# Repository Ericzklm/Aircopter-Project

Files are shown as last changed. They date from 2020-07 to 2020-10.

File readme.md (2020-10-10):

# Aircopter Project

#### To see a more updated version of this project, see Aircopter-Project-v2

This project was done in association with the IEEE Student Branch on the UCLA campus.
This is the first iteration of the project.

The goal of the project was to: 1. Design and assemble a custom PCB for a drone,
2. Write a program to hover the drone, then fly the drone. Because of the nature
of the project, the PCB was required to be small and compact (meaning SMD soldering
was needed) and the program needed to be quick and responsive.

### Hardware Selection Choices:

**MCU**: The main chip is the model STM32F405. This was chosen for its ideal balance
between size and functionality. It is able to support all the needed sensors and
motor drivers for our drone and can be powered by a 3.3v supply which closely
matches the 3.7v of standard drone batteries (3.7v is stepped down to 3.3 using
a voltage regulator). Additionally, this chip was more ideal than other chips of
similar style because it handles floating point calculations better which allows
for simplicity and efficiency when writing the program.

**Voltage Regulator**: The voltage regulator used is the Richtek RT6150B-33GQW which
was choosen for its size and the use of buck-boost as well as operating within
the voltage supplied by the battery. The voltage regulator was simple to use
and had a well documented spec sheet in comparison to other choices but used
exposed pads instead of pins for soldering which proved to be the biggest
challenge in assembly.

**Wireless Module**: The wireless module used is the nrf24l01 which is standard, easy
to use, and familiar so we used it in this application since it fits well with the
acclerometer module.

**Accelerometer/Gyroscope**: The module used is the mpu6050 which is standard, easy to
use, and familiar so we used it in this application since it fits well with the
wireless module.

**Oscillator**: The oscillator used is the Abracon ABLS-12.000MHZ-B2-T which is a
crystal oscillator at 12 mHz which was suitable for the MCU. This specific oscillator
was choosen because the documentation was clear on how to configure the module. A
SMD mounted version was chosen.

**Passive Components**: For the resistors, capacitors, and inductors, we primarily
used parts with the package size 0603 which would fit the board without being
overly difficult to solder. Each piece was checked for its operating voltages as 
well as the operating temperatures to make sure no issues would arise.

### Hardware Design Choices:

**General**: The board is composed of two sides where each side has routes and vias to
connect the different components. The negative spaces are occupied by polygons. On
the front side, there is a seperate polygon for 3.7v and 3.3v that are connected
by the voltage regulator that steps the voltage down. On the back, there are seperate
polygons for ground and motor ground. Motor ground is seperated because the motor
ground will have more noise and we dont want to include the added noise in other
components.

**Battery**: The battery is a generic 3.7v drone battery that connects via a JST connector.
A couple of decoupling capacitors are placed directly alongside the female header on the 
board. It is placed as close as possible to the JST headers that connect to the motors
as we need to decrease the resistance by having a large polygon that gives a direct
connection.

**Voltage Regualtor**: The voltage regulator is placed between the 3.7v and 3.3v planes
such that the two are completely isolated. There is an inductor included directly
alongside the voltage regulator as recommended by the spec sheet. A few decoupling
capcitors are also included.

**Voltage Divider**: A couple resistors are used to form a voltage divider that gives
an analog input to the MCU which can be used to read battery status. These resistors
are placed such that they do not have signficant effect on the routing or the polygons.

**Programmer**: The programmer is a set of 4 male header pins that allow us to upload 
programs to the drone through a seperate board. It is placed in the top left corner
for easy access and to make sure the sensors do not cover the pins.

**Reset Button**: The switch is placed such that there is easy access to it while not having
the placement disrupt any polygons. A capacitor is included to stabalize the signal sent
to the MCU.

**Oscillator**: The oscillator is placed as close to the MCU as possible to reduce unwanted
affects on the traces. As indicated by the spec sheet, there are two resistors that
ground both the input and output of the oscillator.

**Motors**: The motors connectorsare placed along the top of the board for easy access when 
plugging in the JST connectors. Each motor is paired with a motor driver circuit including
a diode and a mosfet. These components are located as close as possible to each other and 
have the thickest possible traces to decrease resistance. Each motor driver is connected
to a PWM capable pin located on the MCU.

**MCU**: The MCU is placed in a central position on the board as it needs to connect to most
components on the board. It is turned such that the length of traces is optimized and
components that are more essential to have short traces are accounted for. The decoupling
capacitors for the MCU are located on the opposite side of it and are connected by vias.

**Sensor Modules**: Both modules are lifted above the board using headers and because they
sit at similar heights above the board, their placement does not overlap. The decoupling
capacitors are placed near the respective pins on the MCU.

### Hardware Flaws:

**Not Space Efficient**: A few choices made the board more cluttered and more difficult to
make routes and polygons. The motor driver circuits could have made better use of the
two sided board as in the current configuration, they occupied a quarter of the board.
The oscillator would have benefitted from being a through-hole component as the soldering
pads and capacitors occupied a lot of space. In a different part of the board. There is
a lot of open space meaning there are parts of the board where there are unnecessary
bottlenecks.

**Accelerometer Placement**: The idea behind the accelerometer and wireless module not
overlapping is that since they were both lifted off the main board at a similar height,
they could not occupy the same space. However, the accelerometer lies slightly lower
than the wireless module so it can be moved closer the the MCU, allowing for shorter
traces.

**Bottlenecks**: There are some moderate bottlenecks in this design and also places where
the polygons have rather indirect routes. For example, some components rely on power
that comes gaps in the MCU which signficantly bottlenecks the polygons. The 3.3v 
needed by the wireless module comes from a couple vias and a route used as a bridge
rather than having a direct connection as it is cut off from the 3.3v polygon.

**Voltage Regulator**: The voltage regulator was small and simple but due to the exposed
pad design and its small size, was a pain to solder. This ended up being by far the
biggest hiccup in the assembly of the board and required backup components.

**Decoupling Capacitors**: The decoupling capacitors are not optimally placed in every
case but rather are placed to prevent bottlenecks. Capacitors for certain components
are placed near the MCU rather than the component itself.

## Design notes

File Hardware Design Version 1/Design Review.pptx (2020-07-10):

## Design Review

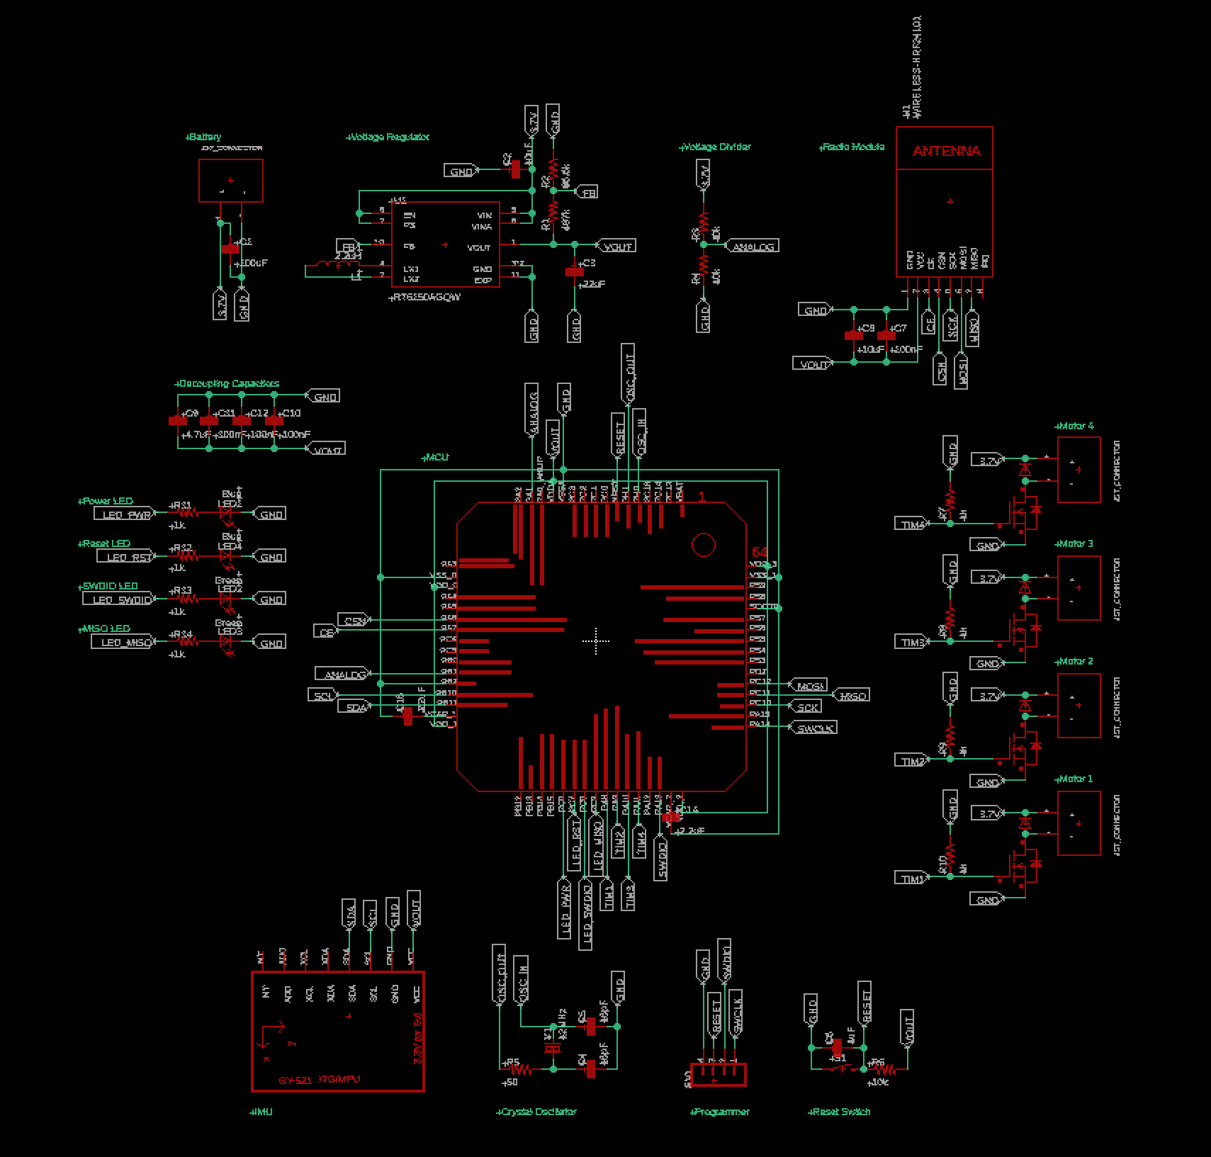
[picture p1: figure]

Team #6

## Parts

Programmer
Oscillator/resonator: ABLS-12.000MHZ-B2-T
Voltage regulator
Decoupling capacitors
Reset switch

Battery: 3.7 Volts
Voltage divider
Radio module: NRF24L01p
IMU: MPU6050
Motor driver (x4)
MCU: STM32F405RGT6

## Battery

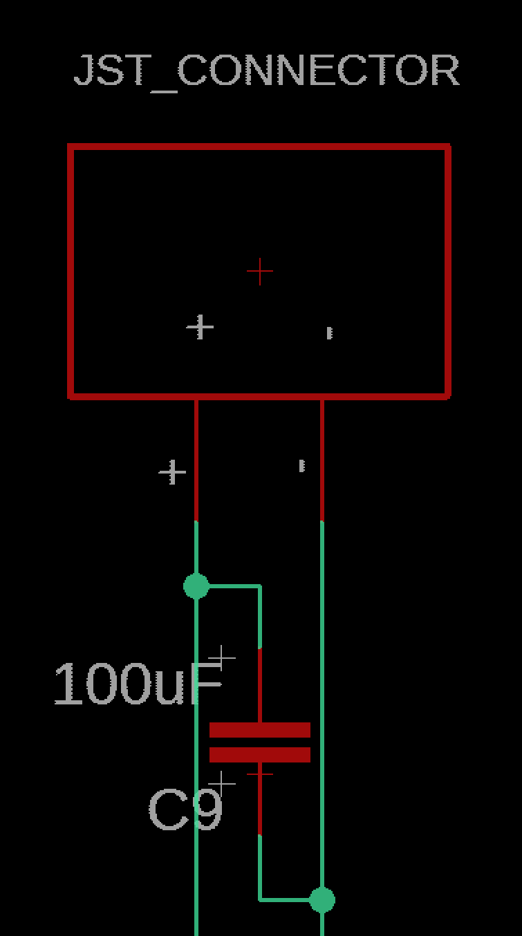
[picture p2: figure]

3.7 V
100 uF Decoupling Capacitor

## Voltage Divider

Resistors: 10kOhm (x2)
Attached to an analog pin
Receives power from the battery

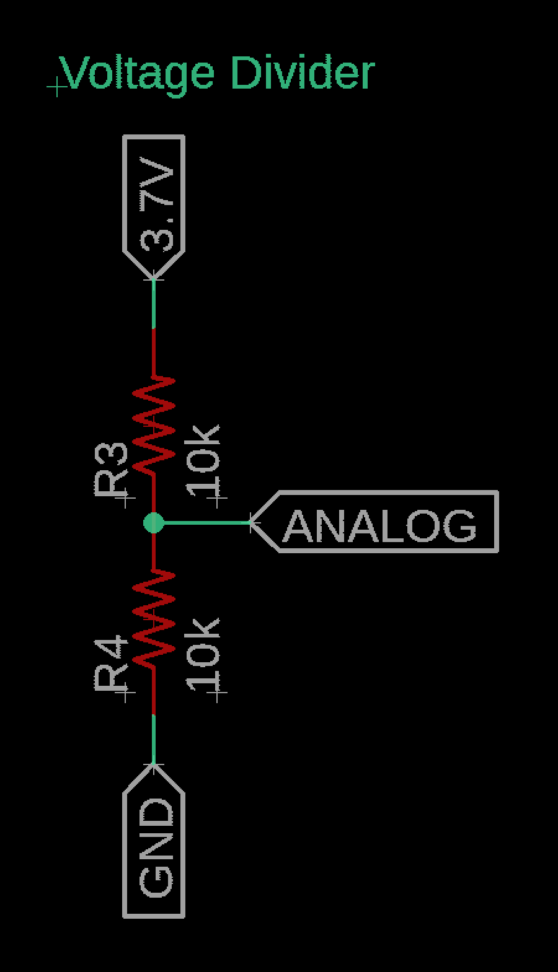
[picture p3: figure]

## Radio Module

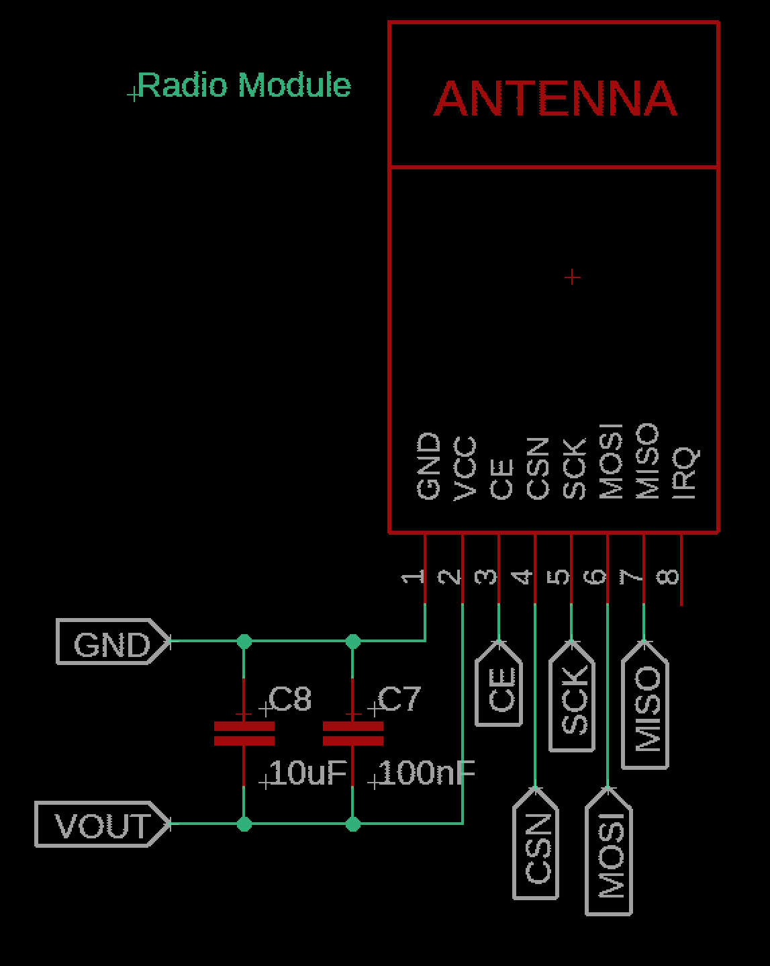
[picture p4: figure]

NRF24L01p
Decoupling Capacitors: 10uF, 100nF

## IMU

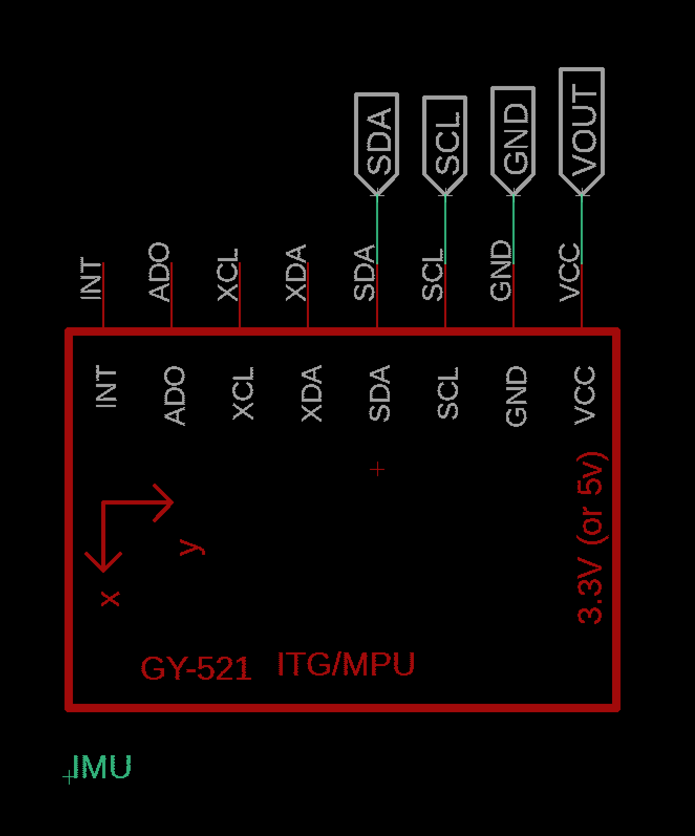
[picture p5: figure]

MPU6050

## Motor Driver

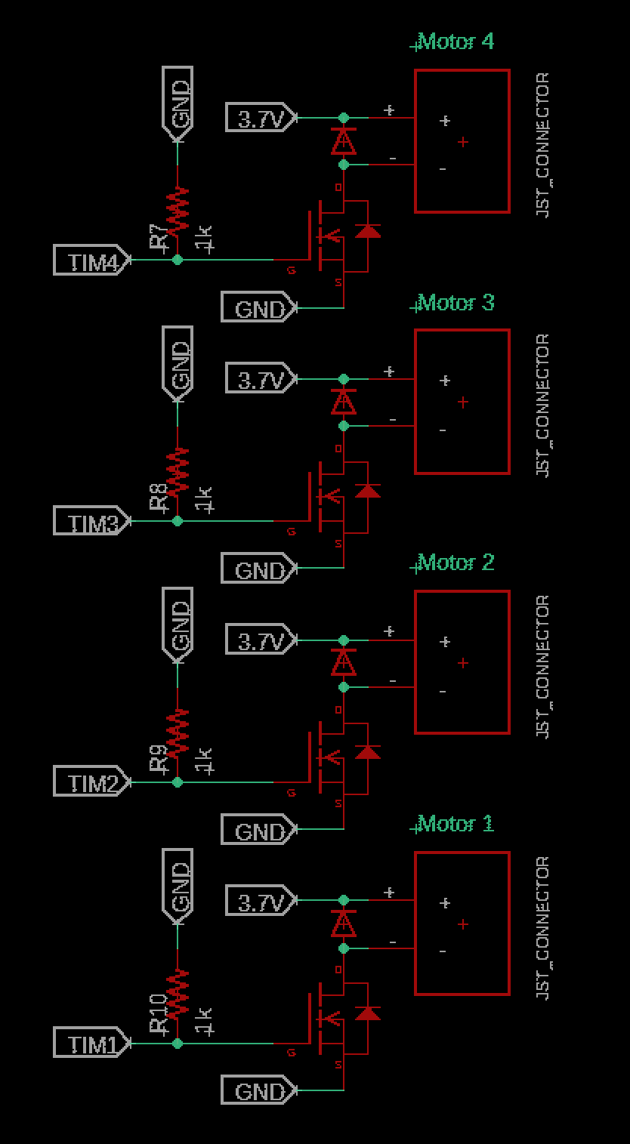
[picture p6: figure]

MOSFET: Infineon IRLML6244TRPBF (x4)
Diode: Panasonic DB2W40300L (x4)
Resistor: 1kOhm (x4)

## MCU

STM32F405RGT6

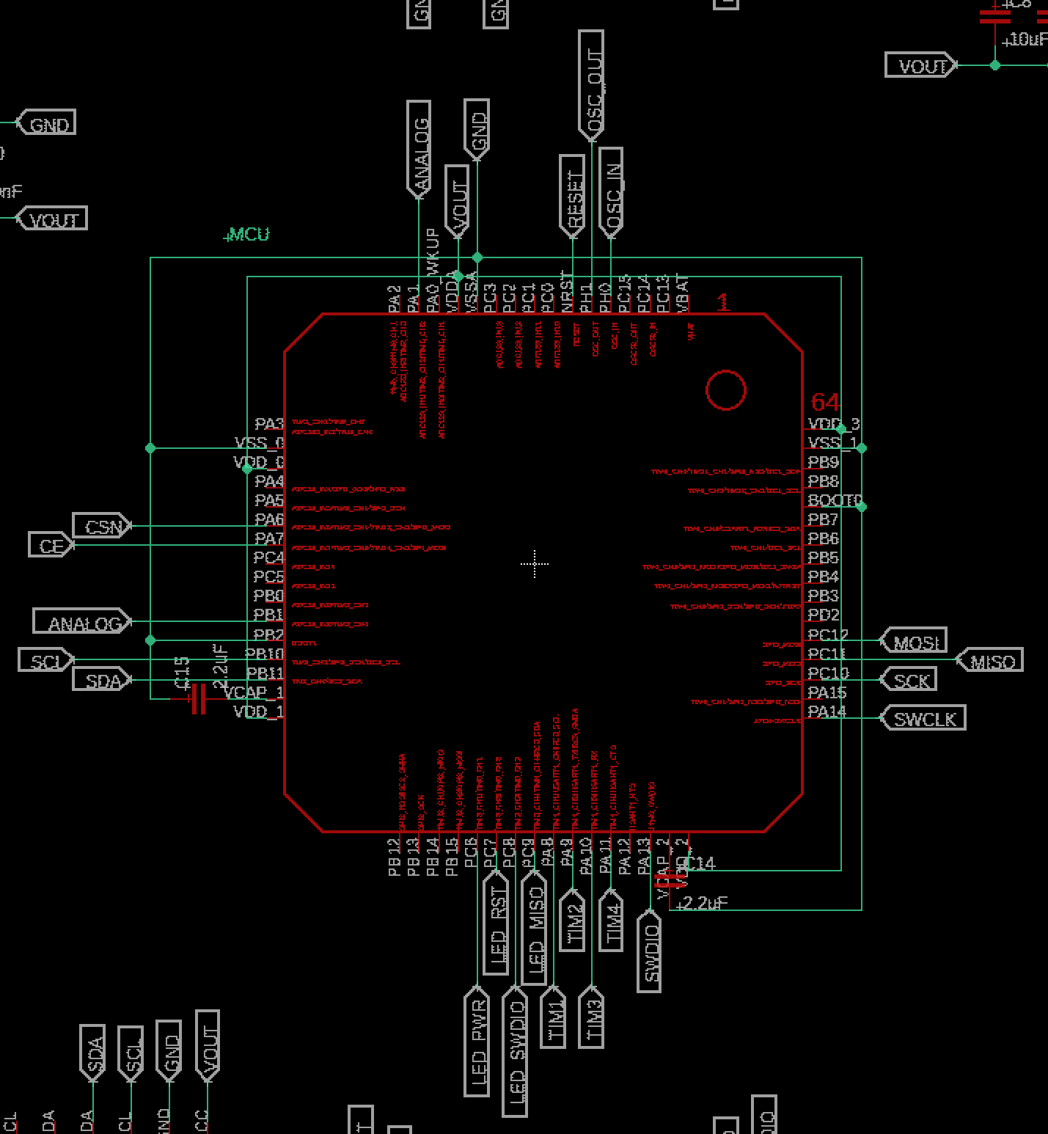
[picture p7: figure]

## Programmer

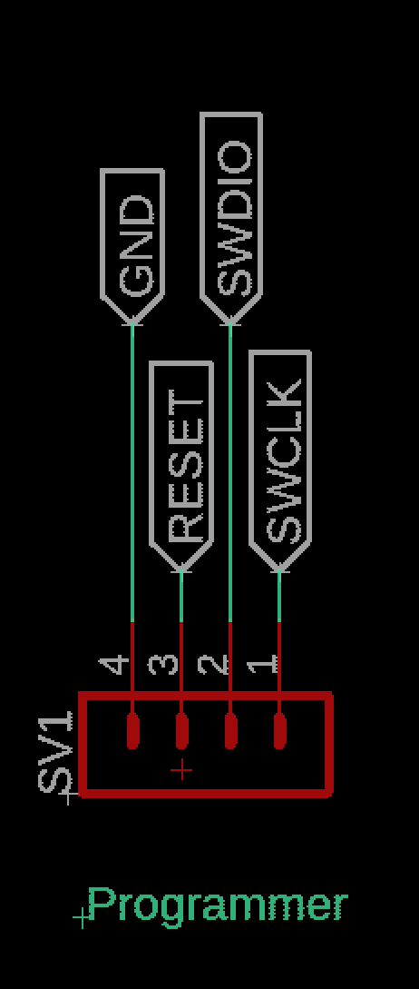
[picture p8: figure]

## Crystal Oscillator

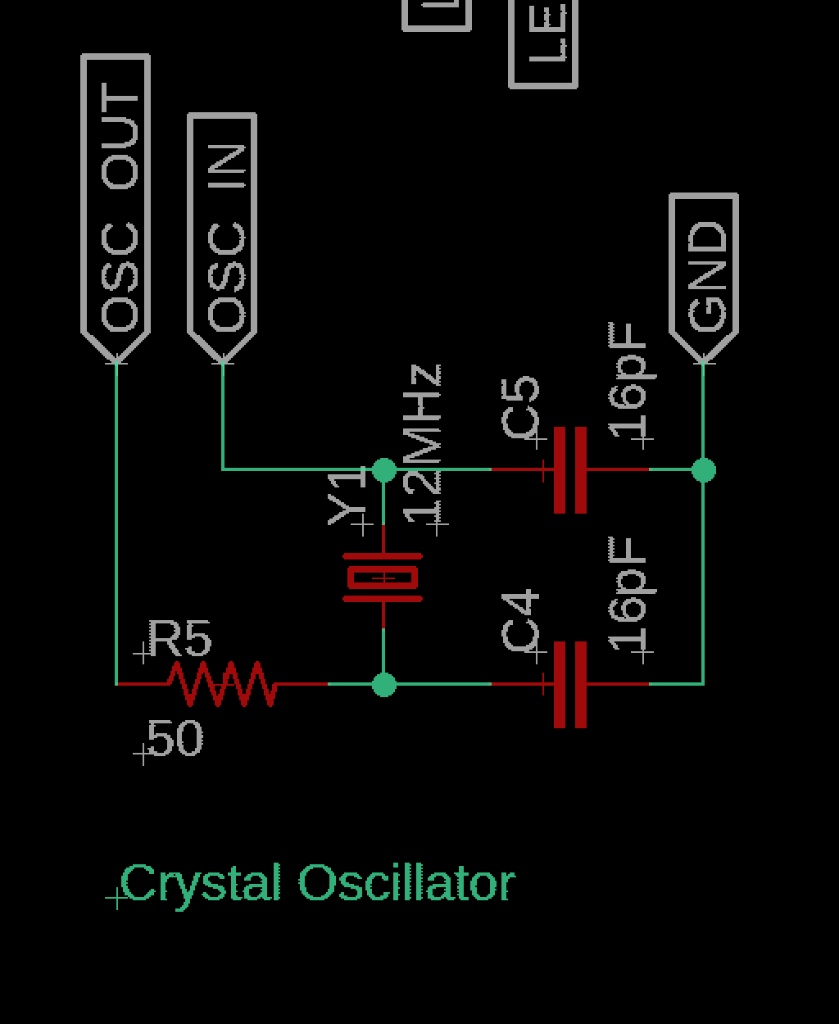
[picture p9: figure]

Abracon ABLS-12.000MHZ-B2-T
Capacitor: 16pF (x2)
Resistor: 50Ohm

## Voltage Regulator

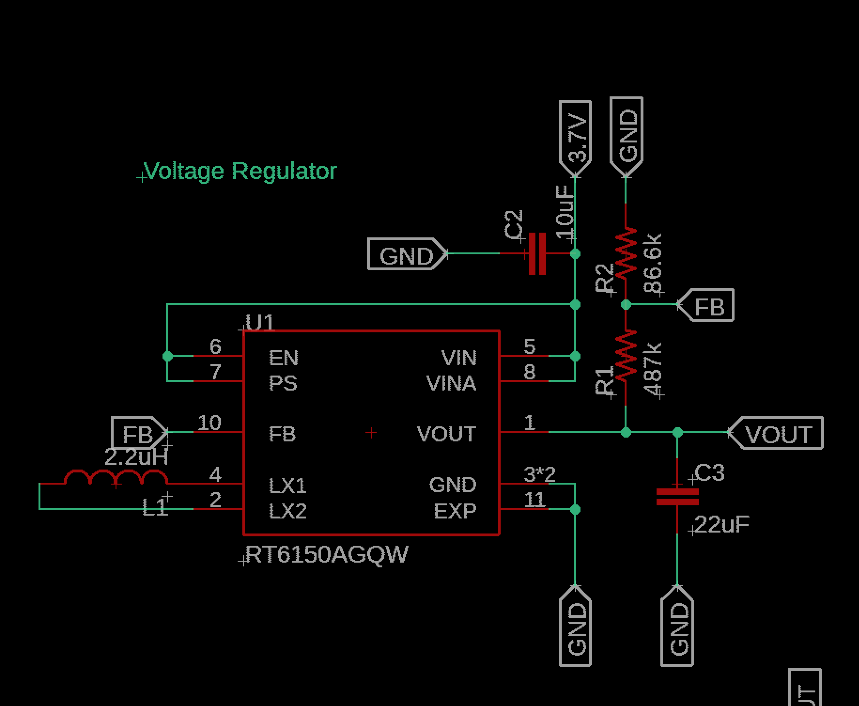
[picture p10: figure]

Richtek RT6150BGQW
Resistors: 487kOhm, 86.6kOhm
Capacitors: 22uF
Inductors: 2.2uH

## Decoupling Capacitors

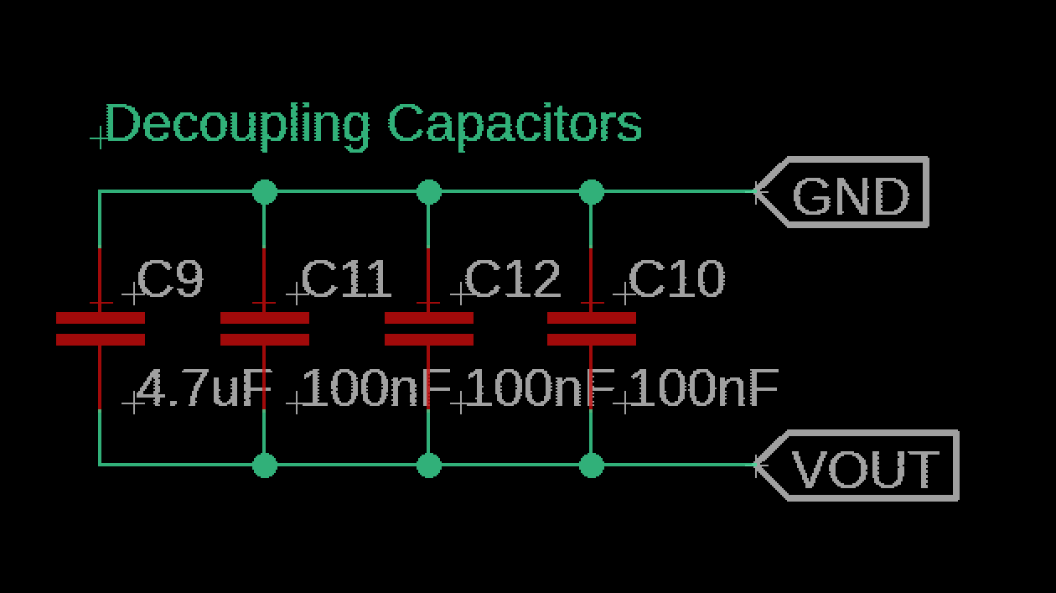
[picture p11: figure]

NRF24L01p
MCU: 100nF (x3), 4.7uF
Battery: 100uF
Radio: 10uF, 100nF
Voltage Regulator: 22uF

## Reset Switch

Resistor: 10kOhm
Capacitor: 1uF

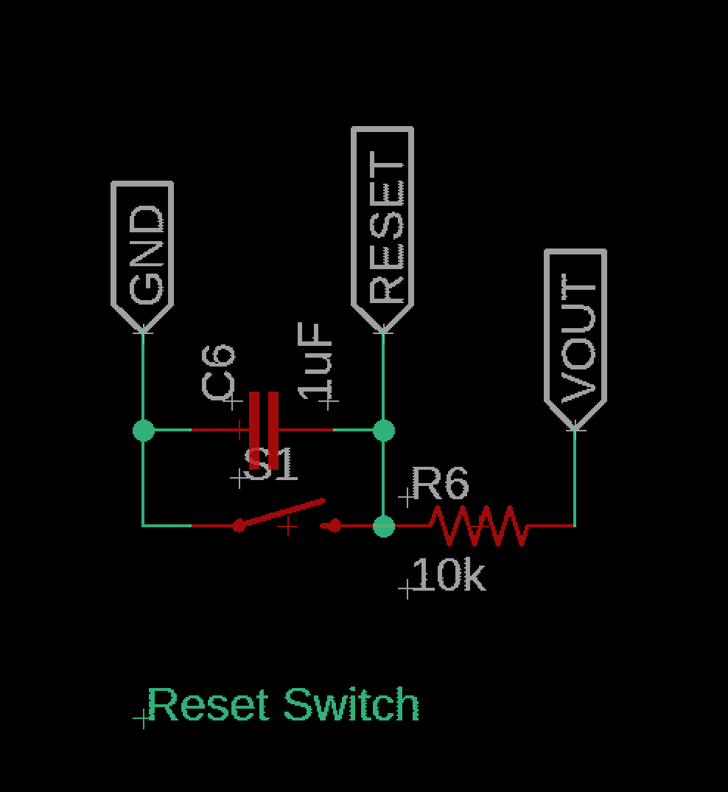
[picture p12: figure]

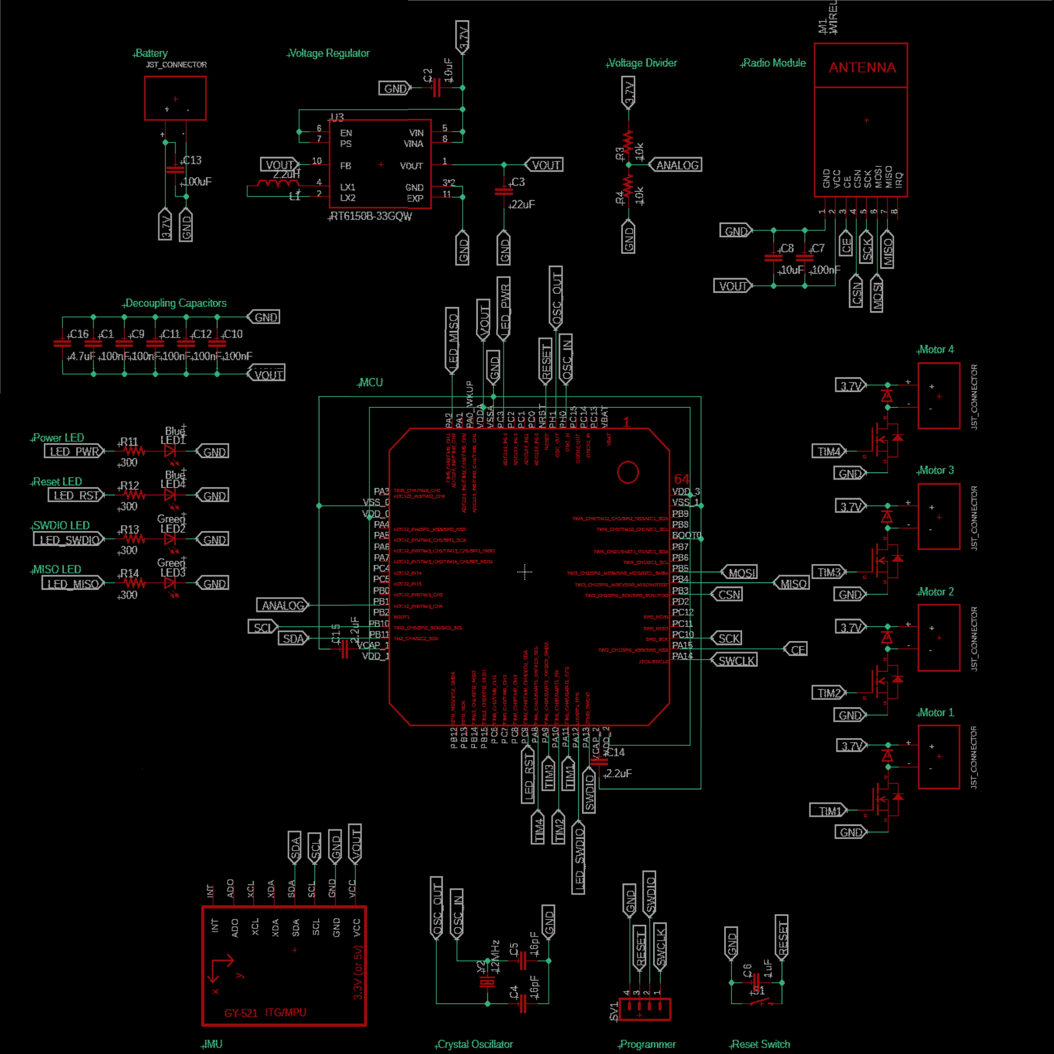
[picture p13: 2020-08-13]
Hardware Design Version 1/Schematic (1).jpg

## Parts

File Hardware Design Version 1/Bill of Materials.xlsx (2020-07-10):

Vendor | Vendor Part # | Manufacturer | Part # | Package | Description | Quantity | Unit Price | Total Cost | Link | Datasheet
Mouser Electronics | 511-STM32F405RGT6 | STMicroelectronics (https://www.mouser.com/stmicroelectronics) | STM32F405RGT6 | LQFP-64 | ARM Microcontrollers - MCU ARM M4 1024 FLASH 168 Mhz 192kB SRAM | 1 | $10.58 | $10.58 | https://www.mouser.com/ProductDetail/STMicroelectronics/STM32F405RGT6?qs=sGAEpiMZZMv%2fbGM7XKYHKw08UF8YuIh3 | https://www.mouser.com/datasheet/2/389/stm32f405rg-956214.pdf | 1
Digi-Key | 535-9067-1-ND | Abracon LLC (https://www.digikey.com/en/supplier-centers/a/abracon) | ABLS-12.000MHZ-B2-T | HC-49/US | CRYSTAL 12.0000MHZ 18PF SMD | 1 | $0.28 | $0.28 | https://www.digikey.com/product-detail/en/abracon-llc/ABLS-12.000MHZ-B2-T/535-9067-1-ND/675584 | https://abracon.com/Resonators/abls.pdf | 1
Digi-Key | 535-12265-1-ND | Abracon LLC | ASMPH-0603-2R2M-T | 0603 (1608 Metric) | FIXED IND 2.2UH 850MA 300 MOHM | 1 | $0.36 | $0.36 | https://www.digikey.com/product-detail/en/abracon-llc/ASMPH-0603-2R2M-T/535-12265-1-ND/4214865 | https://abracon.com/Magnetics/power/ASMPH-0603.pdf | 1
Digi-Key | 1276-1012-1-ND | Samsung Electro-Mechanics (https://www.digikey.com/en/supplier-centers/s/samsung-electro-mechanics-america) | CL10F104ZB8NNNC | 0603 (1608 Metric) | CAP CER 0.1UF 50V Y5V 0603 | 4 | $0.10 | $0.40 | https://www.digikey.com/product-detail/en/samsung-electro-mechanics/CL10F104ZB8NNNC/1276-1012-1-ND/3889098 | http://www.samsungsem.com/kr/support/product-search/mlcc/__icsFiles/afieldfile/2018/07/03/CL10F104ZB8NNNC.pdf | 5
Digi-Key | 1276-6684-1-ND | Samsung Electro-Mechanics (http://www.samsungsem.com/global/index.jsp) | CL10A475MP5LNNC | 0603 (1608 Metric) | CAP CER 4.7UF 10V X5R 0603 | 1 | $0.16 | $0.16 | https://www.digikey.com/product-detail/en/samsung-electro-mechanics/CL10A475MP5LNNC/1276-6684-1-ND/5961543 | http://www.samsungsem.com/kr/support/product-search/mlcc/__icsFiles/afieldfile/2018/06/22/CL10A475MP5LNNC.pdf | 1
Digi-Key | 1276-1119-1-ND | Samsung Electro-Mechanics | CL10A106MQ8NNNC | 0603 (1608 Metric) | CAP CER 10UF 6.3V X5R 0603 | 2 | $0.15 | $0.30 | https://www.digikey.com/product-detail/en/samsung-electro-mechanics/CL10A106MQ8NNNC/1276-1119-1-ND/3889205 | http://www.samsungsem.com/kr/support/product-search/mlcc/__icsFiles/afieldfile/2018/06/20/CL10A106MQ8NNNC.pdf | 2
Digi-Key | 1276-2204-1-ND | Samsung Electro-Mechanics | CL10C160JB8NNNC | 0603 (1608 Metric) | CAP CER 16PF 50V C0G/NP0 0603 | 2 | $0.10 | $0.20 | https://www.digikey.com/product-detail/en/samsung-electro-mechanics/CL10C160JB8NNNC/1276-2204-1-ND/3890290 | http://www.samsungsem.com/kr/support/product-search/mlcc/__icsFiles/afieldfile/2018/06/11/CL10C160JB8NNNC.pdf | 2
Digi-Key | 1276-2868-1-ND | Samsung Electro-Mechanics | CL10A226MQ8NRNE | 0603 (1608 Metric) | CAP CER 22UF 6.3V X5R 0603 | 1 | $0.34 | $0.34 | https://www.digikey.com/product-detail/en/samsung-electro-mechanics/CL10A226MQ8NRNE/1276-2868-1-ND/3890954 | http://www.samsungsem.com/kr/support/product-search/mlcc/__icsFiles/afieldfile/2018/06/20/CL10A226MQ8NRNE.pdf | 1
Digi-Key | 1276-6524-1-ND | Samsung Electro-Mechanics | CL10B105MO8NNWC | 0603 (1608 Metric) | CAP CER 1UF 16V X7R 0603 | 1 | $0.10 | $0.10 | https://www.digikey.com/product-detail/en/samsung-electro-mechanics/CL10B105MO8NNWC/1276-6524-1-ND/5961383 | http://www.samsungsem.com/kr/support/product-search/mlcc/__icsFiles/afieldfile/2018/07/24/CL10B105MO8NNWC.pdf | 1
Digi-Key | 1276-1085-1-ND | Samsung Electro-Mechanics | CL10A225KP8NNNC | 0603 (1608 Metric) | CAP CER 2.2UF 10V X5R 0603 | 2 | $0.12 | $0.24 | https://www.digikey.com/product-detail/en/samsung-electro-mechanics/CL10A225KP8NNNC/1276-1085-1-ND/3889171 | http://www.samsungsem.com/kr/support/product-search/mlcc/__icsFiles/afieldfile/2018/06/20/CL10A225KP8NNNC.pdf | 0
Digi-Key | 490-13982-1-ND | Murata Electronics North America | GRM31CR60J107KE39L | 1206 (3216 Metric) | CAP CER 100UF 6.3V X5R 1206 | 1 | $0.87 | $0.87 | https://www.digikey.com/product-detail/en/murata-electronics-north-america/GRM31CR60J107KE39L/490-13982-1-ND/6155812 | https://search.murata.co.jp/Ceramy/image/img/A01X/G101/ENG/GRM31CR60J107KE39-01.pdf | 1
Mouser Electronics | 71-CRCW060310K0JNEAC | Vishay | CRCW060310K0JNEAC | 0603 (1608 Metric) | Thick Film Resistors 1/10Watt 10Kohms 5% Commercial Use | 2 | $0.17 | $0.34 | https://www.mouser.com/ProductDetail/Vishay/CRCW060310K0JNEAC | https://www.mouser.com/datasheet/2/427/crcwce3-1223726.pdf | 2
~~Mouser Electronics~~ | ~~71-RCP0603W50R0GEB~~ | ~~Vishay/Dale~~ | ~~RCP0603W50R0GEB~~ | ~~0603 (1608 Metric)~~ | ~~Thick Film Resistors 1.5watt 50ohms 2% 0603 WIDE TERM~~ | ~~0~~ | ~~$1.60~~ | ~~$0.00~~ | ~~https://www.mouser.com/ProductDetail/Vishay-Dale/RCP0603W50R0GEB | ~~https://www.mouser.com/datasheet/2/427/rcp-533627.pdf~~ | ~~N~~
~~Digi-Key~~ | ~~TNP100AACT-ND~~ | ~~Vishay/Dale~~ | ~~TNPW0603100RBEEA~~ | ~~0603 (1608 Metric)~~ | ~~RES 100 OHM 0.1% 1/8W 0603~~ | ~~0~~ | ~~$0.65~~ | ~~$0.00~~ | ~~https://www.digikey.com/product-detail/en/vishay-dale/TNPW0603100RBEEA/TNP100AACT-ND/1857056~~ | ~~http://www.vishay.com/docs/28758/tnpw_e3.pdf~~ | ~~N~~
~~Digi-Key~~ | ~~RHM1.0KDCT-ND~~ | ~~Rohm Semiconductor~~ | ~~ESR03EZPJ102~~ | ~~0603 (1608 Metric)~~ | ~~RES SMD 1K OHM 5% 1/4W 0603~~ | ~~0~~ | ~~$0.10~~ | ~~$0.00~~ | ~~https://www.digikey.com/product-detail/en/rohm-semiconductor/ESR03EZPJ102/RHM1.0KDCT-ND/1762924~~ | ~~https://www.rohm.com/datasheet/ESR01MZPF/esr-e~~ | ~~N~~
~~Digi-Key~~ | ~~P487KHCT-ND~~ | ~~Panasonic Electronic Components~~ | ~~ERJ-3EKF4873V~~ | ~~0603 (1608 Metric)~~ | ~~RES SMD 487K OHM 1% 1/10W 0603~~ | ~~0~~ | ~~$0.10~~ | ~~$0.00~~ | ~~https://www.digikey.com/product-detail/en/panasonic-electronic-components/ERJ-3EKF4873V/P487KHCT-ND/198411~~ | ~~https://industrial.panasonic.com/cdbs/www-data/pdf/RDA0000/AOA0000C304.pdf~~ | ~~N~~
~~Digi-Key~~ | ~~P86.6KDBCT-ND~~ | ~~Panasonic Electronic Components~~ | ~~ERA-3AEB8662V~~ | ~~0603 (1608 Metric)~~ | ~~RES SMD 86.6KOHM 0.1% 1/10W 0603~~ | ~~0~~ | ~~$0.35~~ | ~~$0.00~~ | ~~https://www.digikey.com/product-detail/en/panasonic-electronic-components/ERA-3AEB8662V/P86.6KDBCT-ND/3076074~~ | ~~https://industrial.panasonic.com/cdbs/www-data/pdf/RDM0000/AOA0000C307.pdf~~ | ~~N~~
~~Digi-Key~~ | ~~DB2W40300LCT-ND~~ | ~~Panasonic Electronic Components~~ | ~~DB2W40300L~~ | ~~SOD-123F~~ | ~~DIODE SCHOTTKY 40V 3A MINI2~~ | ~~4~~ | ~~$0.60~~ | ~~$2.40~~ | ~~https://www.digikey.com/product-detail/en/panasonic-electronic-components/DB2W40300L/DB2W40300LCT-ND/3884376~~ | ~~https://industrial.panasonic.com/content/data/SC/ds/ds4/DB2W40300L_E.pdf~~ | ~~4~~
Mouser Electronics | 942-IRLML6244TRPBF | Infineon | IRLML6244TRPBF | SOT-23-3 | MOSFET MOSFT 20V 6.3A 21mOhm 2.5V cpbl | 4 | $0.39 | $1.56 | https://www.mouser.com/ProductDetail/942-IRLML6244TRPBF | https://www.mouser.com/datasheet/2/196/irlml6244pbf-1228275.pdf | 4
~~Digi-Key~~ | ~~1028-1259-1-ND~~ | ~~Richtek USA inc~~ | ~~RT6150AGQW~~ | ~~10-WFDFN Exposed Pad (3x3)~~ | ~~IC REG BUCK BST ADJ 0.8A 10WDFN~~ | ~~0~~ | ~~$1.63~~ | ~~$0.00~~ | ~~https://www.digikey.com/product-detail/en/richtek-usa-inc/RT6150AGQW/1028-1259-1-ND/4733181~~ | ~~https://www.richtek.com/assets/product_file/RT6150A=RT6150B/DS6150AB-05.pdf~~ | ~~N~~
~~Digi-Key~~ | ~~311-76.8KHRCT-ND~~ | ~~Yageo~~ | ~~RC0603FR-0776K8L~~ | ~~0603 (1608 Metric)~~ | ~~RES SMD 76.8K OHM 1% 1/10W 0603~~ | ~~0~~ | ~~$0.10~~ | ~~$0.00~~ | ~~https://www.digikey.com/product-detail/en/yageo/RC0603FR-0776K8L/311-76.8KHRCT-ND/730329~~ | ~~http://www.yageo.com/documents/recent/PYu-RC_Group_51_RoHS_L_9.pdf~~ | ~~N~~
Digi-Key | 732-4966-1-ND | Wurth Electronics | 150060BS75000 | 0603 (1608 Metric) | LED BLUE CLEAR 0603 SMD | 2 | $0.16 | $0.32 | https://www.digikey.com/product-detail/en/wurth-electronics-inc/150060VS75000/732-4980-1-ND/4489904 |  | 2
Digi-Key | 732-4980-1-ND | Wurth Electronics | 150060VS75000 | 0603 (1608 Metric) | LED GREEN CLEAR 0603 SMD | 2 | $0.15 | $0.30 | https://www.digikey.com/product-detail/en/wurth-electronics-inc/150060VS75000/732-4980-1-ND/4489904 |  | 2
Digi-Key | RT6150B-33GQWCT-ND | Richtek USA Inc. | RT6150B-33GQW | 10-WFDFN Exposed Pad | IC BUCK-BOOST 0.8A WDFN-10 | 1 | $2.17 | $2.17 | https://www.digikey.com/product-detail/en/richtek-usa-inc/RT6150B-33GQW/RT6150B-33GQWCT-ND/6676777 | https://www.richtek.com/assets/product_file/RT6150A=RT6150B/DS6150AB-05.pdf | 0
Digi-Key | RHM300DCT-ND | Rohm Semiconductor | ESR03EZPJ301 | 0603 (1608 Metric) | RES SMD 300 OHM 5% 1/4W 0603 | 4 | $0.10 | $0.40 | https://www.digikey.com/product-detail/en/rohm-semiconductor/ESR03EZPJ301/RHM300DCT-ND/1762932 | https://www.rohm.com/datasheet/ESR01MZPF/esr-e | 4
Mouser | 652-CD0603-S01575 | Bourns | CD0603-S01575 | 0603 (1608 metric) | Diode | 4 | $0.39 | $1.56 | https://www.mouser.com/ProductDetail/Bourns/CD0603-S01575?qs=FITO%2f%2fQgYDlmbwJLjhqThQ%3d%3d | https://www.mouser.com/datasheet/2/54/D0603_1005-777241.pdf
 |  |  |  |  |  |  |  | 0
 |  |  |  |  |  |  |  | 0
 |  |  |  |  |  |  | Total Cost: | $22.88

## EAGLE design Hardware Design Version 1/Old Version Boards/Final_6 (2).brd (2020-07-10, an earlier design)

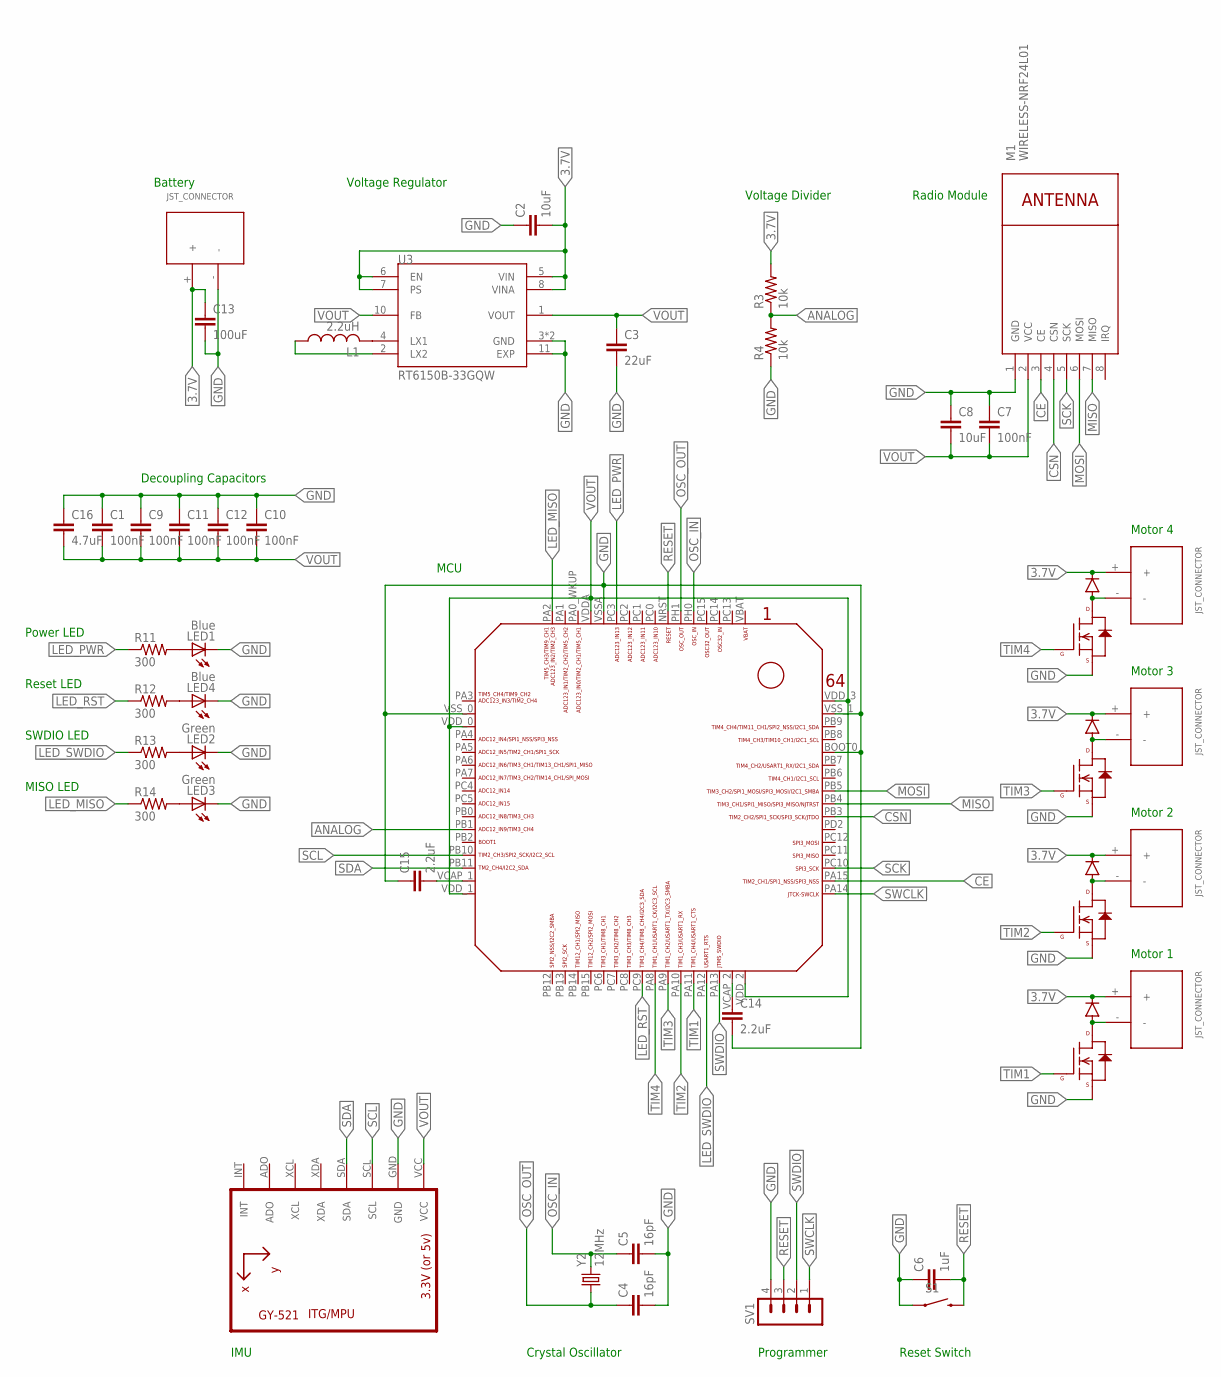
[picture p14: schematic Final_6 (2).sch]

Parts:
C1, C7, C9, C10, C11, C12: 100nF; C0603
C2, C8: 10uF; C0603
C3: 22uF; C0603
C4, C5: 16pF; C0603
C6: 1uF; C0603
C13: 100uF; C1206
C14, C15: 2.2uF; C0603
C16: 4.7uF; C0603
L1: 2.2uH; L0603
LED1, LED4: Blue; CHIP-LED0603
LED2, LED3: Green; CHIP-LED0603
M1: WIRELESS-NRF24L01
R3, R4: 10k; R0603
R11, R12, R13, R14: 300; R0603
S1: SWITCH-MOMENTARY-2SMD; TACTILE-SWITCH-SMD
SV1: MA04-1
U2: GY-521MPU6050; GY-521
U3: RT6150B-33GQW; SON50P250X250X80-11N
U$1: STM32F405/415_LQFP64
U$2, U$3, U$4, U$5, U$6: JST_CONNECTOR_FEMALE
U$7, U$8, U$9, U$10: N-CHANNEL-MOSFET-IRLML6244TRPBF; SOT23-3
U$11, U$12, U$13, U$14: DB2W40300L; MINI2-F3-B
Y2: 12MHz; HC49UP

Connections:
3.7V: C2.2, C13.1, R3.2, U3.5 (VIN), U3.6 (EN), U3.7 (PS), U3.8 (VINA), U$2.+, U$3.+, U$4.+, U$5.+, U$6.+, U$11.NEG (GPIN), U$12.NEG (GPIN), U$13.NEG (GPIN), U$14.NEG (GPIN)
ANALOG: R3.1, R4.2, U$1.PB1
CE: M1.3 (CE), U$1.PA15
CSN: M1.4 (CSN), U$1.PB3
GND: C1.1, C2.1, C3.2, C4.2, C5.2, C6.1, C7.1, C8.1, C9.1, C10.1, C11.1, C12.1, C13.2, C14.2, C15.1, C16.1, LED1.C, LED2.C, LED3.C, LED4.C, M1.1 (GND), R4.1, S1.1, SV1.4, U2.GND, U3.3 (GND), U3.9 (GND), U3.11 (EXP), U$1.BOOT0, U$1.VSSA, U$1.VSS_0, U$1.VSS_1, U$2.-, U$7.2 (S), U$8.2 (S), U$9.2 (S), U$10.2 (S)
LED_MISO: R14.1, U$1.PA2
LED_PWR: R11.1, U$1.PC3
LED_RST: R12.1, U$1.PC9
LED_SWDIO: R13.1, U$1.PA12
MISO: M1.7 (MISO), U$1.PB4
MOSI: M1.6 (MOSI), U$1.PB5
unnamed: L1.2, U3.4 (LX1)
unnamed: L1.1, U3.2 (LX2)
unnamed: U$3.-, U$9.3 (D), U$11.POS (PPIN)
unnamed: U$5.-, U$8.3 (D), U$12.POS (PPIN)
unnamed: U$4.-, U$7.3 (D), U$13.POS (PPIN)
unnamed: U$6.-, U$10.3 (D), U$14.POS (PPIN)
unnamed: LED1.A, R11.2
unnamed: LED4.A, R12.2
unnamed: LED2.A, R13.2
unnamed: LED3.A, R14.2
unnamed: C15.2, U$1.VCAP_1
unnamed: C14.1, U$1.VCAP_2
OSC_IN: C5.1, U$1.PH0, Y2.2
OSC_OUT: C4.1, U$1.PH1, Y2.1
RESET: C6.2, S1.3 (2), SV1.3, U$1.NRST
SCK: M1.5 (SCK), U$1.PC10
SCL: U2.SCL, U$1.PB10
SDA: U2.SDA, U$1.PB11
SWCLK: SV1.1, U$1.PA14
SWDIO: SV1.2, U$1.PA13
TIM1: U$1.PA11, U$10.1 (G)
TIM2: U$1.PA10, U$8.1 (G)
TIM3: U$1.PA9, U$7.1 (G)
TIM4: U$1.PA8, U$9.1 (G)
VOUT: C1.2, C3.1, C7.2, C8.2, C9.2, C10.2, C11.2, C12.2, C16.2, M1.2 (VCC), U2.VCC, U3.1 (VOUT), U3.10 (FB), U$1.VDDA, U$1.VDD_0, U$1.VDD_1, U$1.VDD_2, U$1.VDD_3

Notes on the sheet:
Motor 4
Motor 3
Motor 2
Motor 1
Battery
Voltage Regulator
Voltage Divider
IMU
Decoupling Capacitors
MCU
Radio Module
Crystal Oscillator
Programmer
Reset Switch
Power LED
Reset LED
SWDIO LED
MISO LED

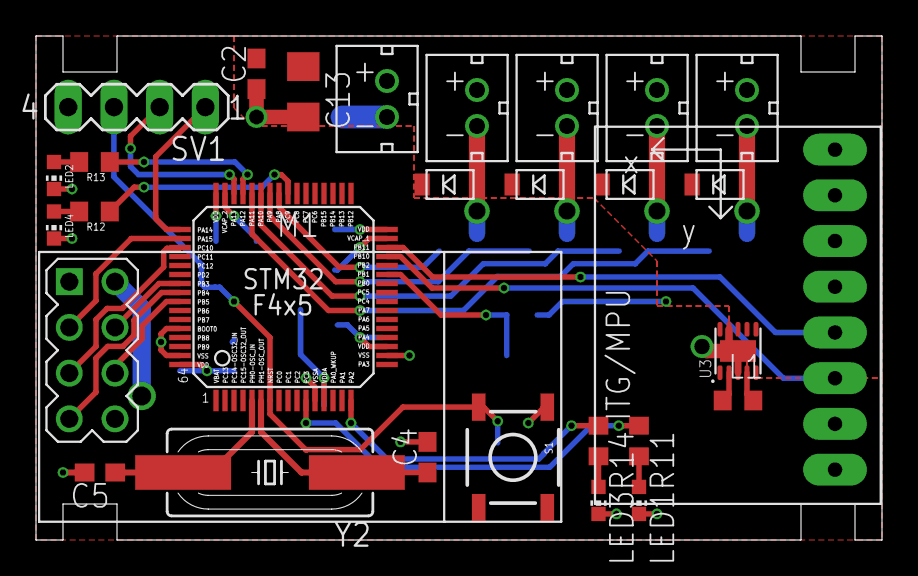
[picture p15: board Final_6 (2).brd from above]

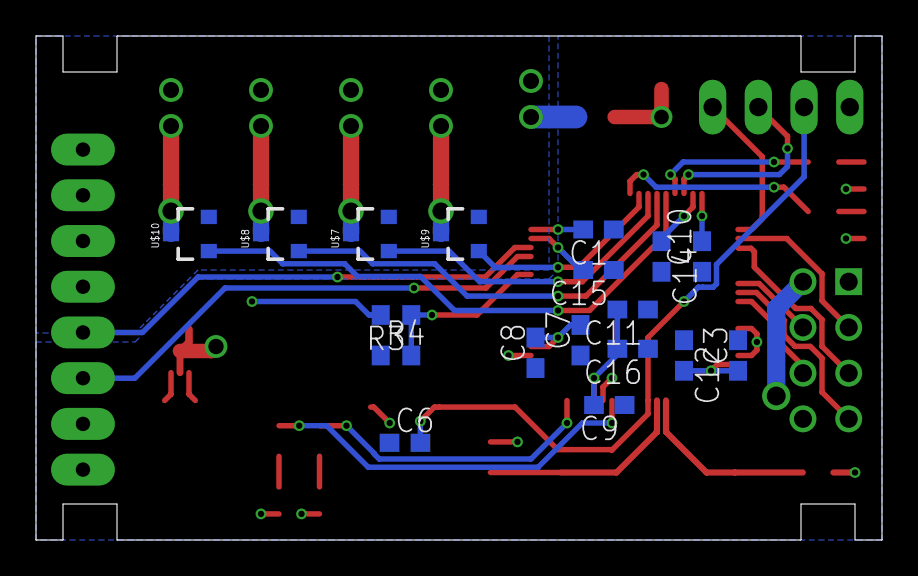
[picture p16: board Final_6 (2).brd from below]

Board: 2 copper layers, 47.0 x 28.0 mm, 47 parts (18 on the bottom side), 36 nets.

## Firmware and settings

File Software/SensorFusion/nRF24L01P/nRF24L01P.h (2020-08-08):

#ifndef __NRF24L01P_H__
#define __NRF24L01P_H__

/**
 * Includes
 */
#include "mbed.h"

/**
 * Defines
 */
#define NRF24L01P_TX_PWR_ZERO_DB         0
#define NRF24L01P_TX_PWR_MINUS_6_DB     -6
#define NRF24L01P_TX_PWR_MINUS_12_DB   -12
#define NRF24L01P_TX_PWR_MINUS_18_DB   -18

#define NRF24L01P_DATARATE_250_KBPS    250
#define NRF24L01P_DATARATE_1_MBPS     1000
#define NRF24L01P_DATARATE_2_MBPS     2000

#define NRF24L01P_CRC_NONE               0
#define NRF24L01P_CRC_8_BIT              8
#define NRF24L01P_CRC_16_BIT            16

#define NRF24L01P_MIN_RF_FREQUENCY    2400
#define NRF24L01P_MAX_RF_FREQUENCY    2525

#define NRF24L01P_PIPE_P0                0
#define NRF24L01P_PIPE_P1                1
#define NRF24L01P_PIPE_P2                2
#define NRF24L01P_PIPE_P3                3
#define NRF24L01P_PIPE_P4                4
#define NRF24L01P_PIPE_P5                5

/**
* Default setup for the nRF24L01+, based on the Sparkfun "Nordic Serial Interface Board"
*  for evaluation (http://www.sparkfun.com/products/9019)
*/
#define DEFAULT_NRF24L01P_ADDRESS       ((unsigned long long) 0xE7E7E7E7E7 )
#define DEFAULT_NRF24L01P_ADDRESS_WIDTH  5
#define DEFAULT_NRF24L01P_CRC            NRF24L01P_CRC_8_BIT
#define DEFAULT_NRF24L01P_RF_FREQUENCY  (NRF24L01P_MIN_RF_FREQUENCY + 2)
#define DEFAULT_NRF24L01P_DATARATE       NRF24L01P_DATARATE_1_MBPS
#define DEFAULT_NRF24L01P_TX_PWR         NRF24L01P_TX_PWR_ZERO_DB
#define DEFAULT_NRF24L01P_TRANSFER_SIZE  4

/**
 * nRF24L01+ Single Chip 2.4GHz Transceiver from Nordic Semiconductor.
 */
class nRF24L01P {

public:

    /**
     * Constructor.
     *
     * @param mosi mbed pin to use for MOSI line of SPI interface.
     * @param miso mbed pin to use for MISO line of SPI interface.
     * @param sck mbed pin to use for SCK line of SPI interface.
     * @param csn mbed pin to use for not chip select line of SPI interface.
     * @param ce mbed pin to use for the chip line.
     * @param irq mbed pin to use for the interrupt request line.
     */
    nRF24L01P(PinName mosi, PinName miso, PinName sck, PinName csn, PinName ce, PinName irq = NC);

    /**
     * Set the RF frequency.
     *
     * @param frequency the frequency of RF transmission in MHz (2400..2525).
     */
    void setRfFrequency(int frequency = DEFAULT_NRF24L01P_RF_FREQUENCY);

    /**
     * Get the RF frequency.
     *
     * @return the frequency of RF transmission in MHz (2400..2525).
     */
    int getRfFrequency(void);

    /**
     * Set the RF output power.
     *
     * @param power the RF output power in dBm (0, -6, -12 or -18).
     */
    void setRfOutputPower(int power = DEFAULT_NRF24L01P_TX_PWR);

    /**
     * Get the RF output power.
     *
     * @return the RF output power in dBm (0, -6, -12 or -18).
     */
    int getRfOutputPower(void);

    /**
     * Set the Air data rate.
     *
     * @param rate the air data rate in kbps (250, 1M or 2M).
     */
    void setAirDataRate(int rate = DEFAULT_NRF24L01P_DATARATE);

    /**
     * Get the Air data rate.
     *
     * @return the air data rate in kbps (250, 1M or 2M).
     */
    int getAirDataRate(void);

    /**
     * Set the CRC width.
     *
     * @param width the number of bits for the CRC (0, 8 or 16).
     */
    void setCrcWidth(int width = DEFAULT_NRF24L01P_CRC);

    /**
     * Get the CRC width.
     *
     * @return the number of bits for the CRC (0, 8 or 16).
     */
    int getCrcWidth(void);

    /**
     * Set the Receive address.
     *
     * @param address address associated with the particular pipe
     * @param width width of the address in bytes (3..5)
     * @param pipe pipe to associate the address with (0..5, default 0)
     *
     * Note that Pipes 0 & 1 have 3, 4 or 5 byte addresses,
     *  while Pipes 2..5 only use the lowest byte (bits 7..0) of the
     *  address provided here, and use 2, 3 or 4 bytes from Pipe 1's address.
     *  The width parameter is ignored for Pipes 2..5.
     */
    void setRxAddress(unsigned long long address = DEFAULT_NRF24L01P_ADDRESS, int width = DEFAULT_NRF24L01P_ADDRESS_WIDTH, int pipe = NRF24L01P_PIPE_P0);

    void setRxAddress(unsigned long msb_address, unsigned long lsb_address, int width, int pipe = NRF24L01P_PIPE_P0);

    /**
     * Set the Transmit address.
     *
     * @param address address for transmission
     * @param width width of the address in bytes (3..5)
     *
     * Note that the address width is shared with the Receive pipes,
     *  so a change to that address width affect transmissions.
     */
    void setTxAddress(unsigned long long address = DEFAULT_NRF24L01P_ADDRESS, int width = DEFAULT_NRF24L01P_ADDRESS_WIDTH);

    void setTxAddress(unsigned long msb_address, unsigned long lsb_address, int width);

    /**
     * Get the Receive address.
     *
     * @param pipe pipe to get the address from (0..5, default 0)
     * @return the address associated with the particular pipe
     */
    unsigned long long getRxAddress(int pipe = NRF24L01P_PIPE_P0);

    /**
     * Get the Transmit address.
     *
     * @return address address for transmission
     */
    unsigned long long getTxAddress(void);

    /**
     * Set the transfer size.
     *
     * @param size the size of the transfer, in bytes (1..32)
     * @param pipe pipe for the transfer (0..5, default 0)
     */
    void setTransferSize(int size = DEFAULT_NRF24L01P_TRANSFER_SIZE, int pipe = NRF24L01P_PIPE_P0);

    /**
     * Get the transfer size.
     *
     * @return the size of the transfer, in bytes (1..32).
     */
    int getTransferSize(int pipe = NRF24L01P_PIPE_P0);


    /**
     * Get the RPD (Received Power Detector) state.
     *
     * @return true if the received power exceeded -64dBm
     */
    bool getRPD(void);

    /**
     * Put the nRF24L01+ into Receive mode
     */
    void setReceiveMode(void);

    /**
     * Put the nRF24L01+ into Transmit mode
     */
    void setTransmitMode(void);

    /**
     * Power up the nRF24L01+ into Standby mode
     */
    void powerUp(void);

    /**
     * Power down the nRF24L01+ into Power Down mode
     */
    void powerDown(void);

    /**
     * Enable the nRF24L01+ to Receive or Transmit (using the CE pin)
     */
    void enable(void);

    /**
     * Disable the nRF24L01+ to Receive or Transmit (using the CE pin)
     */
    void disable(void);

    /**
     * Transmit data
     *
     * @param pipe is ignored (included for consistency with file write routine)
     * @param data pointer to an array of bytes to write
     * @param count the number of bytes to send (1..32)
     * @return the number of bytes actually written, or -1 for an error
     */
    int write(int pipe, char *data, int count);
    
    /**
     * Receive data
     *
     * @param pipe the receive pipe to get data from
     * @param data pointer to an array of bytes to store the received data
     * @param count the number of bytes to receive (1..32)
     * @return the number of bytes actually received, 0 if none are received, or -1 for an error
     */
    int read(int pipe, char *data, int count);

    /**
     * Determine if there is data available to read
     *
     * @param pipe the receive pipe to check for data
     * @return true if the is data waiting in the given pipe
     */
    bool readable(int pipe = NRF24L01P_PIPE_P0);

    /**
     * Disable all receive pipes
     *
     * Note: receive pipes are enabled when their address is set.
     */
    void disableAllRxPipes(void);
    
    /**
     * Disable AutoAcknowledge function
     */
    void disableAutoAcknowledge(void);
    
    /**
     * Enable AutoAcknowledge function
     *
     * @param pipe the receive pipe
     */
    void enableAutoAcknowledge(int pipe = NRF24L01P_PIPE_P0);
    
    /**
     * Disable AutoRetransmit function
     */
    void disableAutoRetransmit(void);
    
    /**
     * Enable AutoRetransmit function
     *
     * @param delay the delay between restransmits, in uS (250uS..4000uS)
     * @param count number of retransmits before generating an error (1..15)
     */
    void enableAutoRetransmit(int delay, int count);

private:

    /**
     * Get the contents of an addressable register.
     *
     * @param regAddress address of the register
     * @return the contents of the register
     */
    int getRegister(int regAddress);

    /**
     * Set the contents of an addressable register.
     *
     * @param regAddress address of the register
     * @param regData data to write to the register
     */
    void setRegister(int regAddress, int regData);

    /**
     * Get the contents of the status register.
     *
     * @return the contents of the status register
     */
    int getStatusRegister(void);

    SPI         spi_;
    DigitalOut  nCS_;
    DigitalOut  ce_;
    InterruptIn nIRQ_;

    int mode;

};

#endif /* __NRF24L01P_H__ */

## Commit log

2020-07-10 Version 1 Hardware Design Files Added
    [1_AnEffortWasMade.brd, 2_NoEffortWasMade.brd, Bill of Materials.xlsx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]
2020-08-13 Added Schematic Image.
